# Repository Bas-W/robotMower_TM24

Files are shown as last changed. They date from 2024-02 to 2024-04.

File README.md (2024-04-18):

# robotMower_TM24
Robot lawn mower project for school.

# Notes
Some notes including the lessons we learned and the mistakes we found in our work can be found under [<b>*/Notes*</b>](/Notes.md)\
This contains some important information for anyone who wants to expand this project, **Please read this document**.

# Features
A list of features can be found under [<b>*/Features*</b>](/Features.md)

# Schematics, PCB
Schematics, along with footprints, can be found under [<b>*/Schematics*</b>](/Schematics).
These are designed in Fusion 360/Eagle, original Fusion/eagle Schematic, board and library files can be found under [***/Schematics/RoborMower_TM24/***](/Schematics/RoborMower_TM24/)

# Code
Code can be found under [***/Code***](/Code).
The final code for the ESP32 can be found under [***/Code/Final_V1.0***](/Code/Final_V1.0.0/).
The final code for the Attiny that read the HC-SR04 sensor can be fount under [***/Code/Test Sketches/ATtiny84_I2C-Slave-Ultrasonic_Test/***](/Code/Test%20Sketches/ATtiny84_I2C-Slave-Ultrasonic_Test/).

# Harware
A list of used components and modules will be made when the design is finalized.

# I²C Adress List
|Part|Address|
|----|---|
|Current Sensor, Motor L|01000000 = 0x40|
|Current Sensor, Motor R|01000001 = 0x41|
|Current Sensor, Bat in|01000010 = 0x42|
|Current Sensor, 5V|01000011 = 0x43|
|Current Sensor, 3V3|01000100 = 0x44|
|Attiny, Ultrasone Sensors|00001000 = 0x8|

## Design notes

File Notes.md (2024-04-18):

# Belangrijke info / gemaakte fouten

# Motor driver
*Gemaakt door Bas Welters.*

Voor dit project maakten we zelf een H-brug om de motors aan te sturen.
Deze H-brug is opgesteld uit MOSFETs en zou aangestuurd worden via een Attiny die op een I²C-bus aangesloten is.

Bij het ontwerpen van de H-brug koos ik echter voor de foute soort MOSFET's voor de high-side switches. Ik gebruik hiervoor NPN-MOSFET's i.p.v. PNP-MOSFET's.
Het ontwerp werkte om de motors aan te sturen maar ik kon niet genoeg spanning doorlaten omdat de gate-spanning op de high-side MOSFET's niet hoog genoeg was. (5V i.p.v. groter dan 12V).
We kozen ervoor om een pre-made H-brug te gebruiken maar het zou wel handig geweest zijn om onze eigen module te gebruiken.
Op de motor driver staan ook twee IC's om het stroomverbruik en de spanning te meten voor elke motor.

# Power-board
*Gemaakt door Bas Welters.*

Op het power-board wordt de batterijspanning omgezet naar 5v en 3.3V.
Dit doen we met LM1117T IC's.
Het bord is bedoeld om gevoedt te worden door een 3S LIPO-batterij.

Om de cellen van de batterij apart uit te meten is ook een JST-poort voorzien. Deze kan echter nog niet gebruikt worden omdat de spanning te hoog is om rechtstreeks uit te lezen met de Attiny.
Om deze poort te kunnen gebruiken zou een tussenstuk gemaakt kunnen worden met spanningsdelers om de spanning binnnen het bereik van de Attiny te brengen.
De Attiny op het power-bord kan met de ESP-32 communiceren via de I²C-bus.

# MCU
*Gemaakt door Nick Bosschaert*

Het MCU-board is de brains van de Robot Mower. Hier worden alle signalen van de sensoren ontvangen en worden alle actuatoren naar behoren aangestuurd. De microcontroller die we plaatsten op dit board is de *ESP32S3 Wroom-1-N8R8*. Dit is de chip die gebruikt wordt op het esp32s3 development board.

Aangezien er eerst voorzien was om een custom H-brug te maken en deze via I²C te verbinden waren er geen connecties voorzien om de originele H-brug te gebruiken. Er zijn echter nog wat extra IO-pins voorzien voor uitbreidingen, deze pins konden we dus gebruiken om de H-brug rechtstreeks aan te sturen met de ESP.

Alle communicatie tussen de mcu en de andere componenten zoals powerboard, hc-sr04 ultrasonic sensors, etc. wordt mogelijk gemaakt door een I²C bus. Deze bus laat ons toe om zowel berichten te ontvangen als te sturen naar geconnecteerde devices. De bus-connector bevat zowel een 5V als 3V3 pin om het gebruik van verschillende sensoren mogelijk te maken. Deze bus wordt dus ook gebruikt om de externe modules van stroom te voorzien.
De SCL en SDA lijnen van deze bus hebben zoals het hoort een pullup naar 3V3. Verbindt deze lijnen **NOOIT** met 5V, want dan zal de esp32 kortgesloten worden. Aangezien I²C werkt met een pulldown om een digitale 1 door te sturen, is dit geen probleem zolang de devices op de bus een digitale 1 lezen op een lager voltage dan 3V3.

Dit board bevat ook een USB-B connector. Deze wordt gebruikt voor het uploaden van nieuwe programmas naar de ESP32 en om gebruik te maken van de seriële monitor.

Veel sensoren en IC's werken met I²C, maar er is ook een connector voorzien voor SPI om bijvoorbeeld een SD-Card te gebruiken om data op op te slaan.

# HC-SR04 Ultrasonic Sensor
*Gemaakt door Nick Bosschaert*

Dit board zorgt ervoor dat er wat druk van de MCU afgehaald wordt door de 3 HC-SR04 afstandssensoren in te laten lezen door een ATTiny. Hierdoor kan het programma op de ESP32 verkleind en de werkdruk verlaagd worden.

De Attiny heeft zelf geen interne timer, waardoor de sensoren niet op de normale manier uitgelezen kunnen worden. Daarom wordt de "NewPing" library gebruikt, deze library laat je toe om toch een timer te gebruiken op de Attiny.
Als de MCU dan een request doet voor 11 bytes aan data, dan stuurt de ATTINY dit geformatteerd door.
Het is tot op heden nog niet mogelijk om een serial output te krijgen van de attiny, een mogelijke oplossing zou zijn om virtueel een UART poort aan te maken en deze via de UART-to-USB chip van een arduino uno of dergelijke te laten gaan.

Het pcb is heel basic met enkel het broodnodige voor de ATTiny om te kunnen draaien, de 2 I²C connectors om door te kunnen verbinden en de 3 connectors voor de HC-SR04 afstandssensoren. Behalve dan dat de lay-out verbeterd zou kunnen worden, is dit een geslaagd ontwerp.

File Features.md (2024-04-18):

# robotMower_TM24
Robot lawn mower project for school.

# Possible Components

|Component|Feature|Digital IO|Analog IO|Multiply|
|---|---|---|---|---|
|HC-SR04 Ultra Sonic|Collision Avoidance|2|0|3|
|Bumper Microswitch|Collision Detection|1|0|2|
|LCD|Interface|2 I2C|0|1|
|Control buttons|Interface|1|0|4|
|Voltage Meter/resistors|Battery Percentage Readout|0|1|1|
|Blades motor|Grass Cutting|3|0|1
|Motor Driver|Driving|6|0|1|
|RTC|Time Control|2 I2C|0|1|
|QMC5883 Kompas||2 I2C|0|1|
|Rocker Switch|Main Power Switch|0|0|1|
|Relay|Emergency Stop/Power Cutoff|2|0|1|
|Axial sensor|Tilt Sensor|x|x|1|
|LM1117 T5.0 LDO|5V Regulation|0|0|1|
|LM1117 T3.3 LDO|3V Regulation|0|0|1|
|Water Sensor|Rain Detection|0|1|1|
|ATtiny84|Breakout µControllers|2 I2C|0|2|
|USB-B|USB-Port|2|0|1|

# Current Features
- [x] Internal 5V Regulation
- [x] Internal 3V3 Regulation
- [x] Current, Voltage, Wattage sensing Battery power
- [x] Current, Voltage, Wattage sensing 5V power
- [x] Current, Voltage, Wattage sensing 3V3 power
- [x] Custom PCB
- [x] Easily Controllable Interface (lcd/oled etc)
- [x] Main Power switch
- [x] USB-connector for programming & monitoring (USB-B / USB-C)
- [x] JST
- [x] Seperate boards - connected via [5v,3v3,I²C]bus
  - MCU
  - Power
  - Sensors

# Possible Features
- [ ] Driving
- [ ] Grass Cutting
- [ ] Power cutoff relay to take away power to motors / emergency stop button (in case of rogue robot event) 
- [ ] Current Measuring for wheels
- [ ] Current Measuring for Blade
- [ ] Collision Avoidance
- [ ] Collision Detection
- [ ] Rain Detection
- [ ] Time Control
- [ ] Small Formfactor
- [ ] Power supply -> 3S/4S LiPo pack ?
- [ ] Battery Charging
- [ ] Battery Percentage Readout
- [ ] Extra I-O for expansions
- [ ] Tilt sensor/switches 
- [ ] Custom H-bridge
- [ ] SD-card slot
- [ ] Temperature sensors for motors (expansion)
- [ ] Temperature sensors for motor drivers (expansion)
- [ ] GPS (u-blox module) (expansion)
- [ ] Perimeter wire (expansion)

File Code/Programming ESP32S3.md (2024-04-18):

# How to Program the ESP32S3 Wroom 1 N8R8

## Connections to ESP32 Dev module
### UART
|ESP32S3|ESP32 Dev Module|
|---|---|
|3V3|3V3|
|GND|GND|
|RX|RX|
|TX|TX|

Connect the ESP32 Dev Module's EN pin to GND.

### USB
Or you can use the USB-B jack to connect straight to your laptop.
Don't forget to enable ***USB CDC On Boot*** in the tools menu.

## Programming ESP32S3
Board: ESP32S3 Dev Module

1. Press and hold the Boot Button.
2. Press and Release the EN/Reset Button.
3. Release the Boot Button.

Upload the program to the ESP32 Dev Module and after the upload is compleet, press the reset button once more so that the ESP32S3 will be reset.

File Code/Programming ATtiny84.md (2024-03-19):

# How to Program the ATtiny84

[example](https://www.instructables.com/Arduino-Uno-to-Program-ATTINY84-Arduino-V-185/)

## Setup
Additional boards: http://drazzy.com/package_drazzy.com_index.json
Upload the ArduinoISP sketch from the example sketches to the Uno.

## Connections to UNO
|ATtiny84|UNO|
|---|---|
|5V|5V|
|GND|GND|
|Pin4|Pin10|
|Pin7|Pin11|
|Pin8|Pin12|
|Pin9|Pin13|

Connect UNO RESET pin to GND via 10uF Elec Cap.

## Programming ATtiny84
Board: ATtiny84
B.O.D.: Disable
LTO: Disable
Pin Mapping: Counter Clockwise
Chip: ATtiny84
Clock: 8MHz Internal
Bootloader: Burn Bootloader
Programmer: Arduino as ISP

To program the attiny you have to use *Upload Using Programmer* or shortcut *Ctrl + Shift + U* otherwise the preselected programmer won't be used.

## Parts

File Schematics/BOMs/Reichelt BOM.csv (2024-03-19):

Qty | Ultrasonic | MCU | Motor | Power | Reserve | Value | Device | Package | Parts | Description | MANUFACTURER_NAME | MANUFACTURER_PART_NUMBER | Reichelt_PART_NUMBER
7 | 3 |  |  | 1 | 3 | JST XH 4-PIN | JST-XH-04-PIN-LONG-PAD | JST-XH-04-PACKAGE-LONG-PAD |  |  |  |  | JST XH4P ST
7 | 3 |  |  | 1 | 3 | Female |  |  |  |  |  |  | JST XH4P BU
15 | 2 | 4 | 2 | 2 | 5 | JST XH 5-PIN | JST-XH-05-PIN-LONG-PAD | JST-XH-05-PACKAGE-LONG-PAD |  |  |  |  | JST XH5P ST
15 | 2 | 4 | 2 | 2 | 5 | Female |  |  |  |  |  |  | JST XH5P BU
66 | 22 | 20 | 10 | 14 | 34 | Krimp Klipkes |  |  |  |  |  |  | JST XH CKB

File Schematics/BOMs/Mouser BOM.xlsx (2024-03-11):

Qty | Ultrasonic | MCU | Motor | Power | Reserve | Value | Device | Package | Parts | Description | MANUFACTURER_NAME | MANUFACTURER_PART_NUMBER | MOUSER_PART_NUMBER
20 | 2 | 3 | 4 | 5 | 6 | 0.1uF | C-EU025-030X050 | C025-030X050 | CAPACITOR, European symbol |  | Murata Electronics | RDER71E104K0P1H03B | 81-RDER71E104K0P1H3B
10 | 1 | 1 | 1 | 5 | 2 | 10uF | CPOL-EUE5-10.5 | E5-10,5 | POLARIZED CAPACITOR, European symbol |  | Würth Elektronik | "870575873001" | 710-870575873001
10 |  |  | 2 | 3 | 5 | 220Ohm | R-EU_0204/7 | 0204/7 | RESISTOR, European symbol |  | KOA Speer (https://www.mouser.be/manufacturer/koa-speer/) | MF1/4CCT52R2200F | 660-MF1/4CCT52R2200F
10 | 1 | 2 | 1 | 1 | 5 | 10kOhm | R-EU_0204/7 | 0204/7 | RESISTOR, European symbol |  | KOA Speer (https://www.mouser.be/manufacturer/koa-speer/) | MF1/4LCT52R103G | 660-MF1/4LCT52R103G
5 |  | 2 |  |  | 3 | 2k2 | R-EU_0204/5 | 0204/5 | RESISTOR, European symbol |  | KOA Speer (https://www.mouser.be/manufacturer/koa-speer/) | MF1/4DCT52R2201F | 660-MF1/4DCT52R2201F
6 |  |  | 2 | 2 | 2 | 12mOhm | R-EU_0204/7 | 0204/7 | RESISTOR, European symbol |  | YAGEO | ERJ-6CWDR012V | 667-ERJ-6CWDR012V
5 |  |  |  | 2 | 3 | 39mOhm | R-EU_0204/7 | 0204/7 | RESISTOR, European symbol |  | YAGEO | PE2512DKE070R04L | 603-PE2512DKE070R04L
2 |  | 1 |  |  | 1 | USB_B_PTH | USB-B-PTH | USB Type B Connector |  |  | CUI Devices | UJ2-B-HR-G-TH | 179-UJ2-B-HR-G-TH
10 | 1 | 2 | 1 | 1 | 5 | button | SWITCH_PUSHBUTTONEVQ-PE | TACT_PANA-EVQ | Buttons |  | TE Connectivity / Alcoswitch | FSMCH | 506-FSMCH
5 | 1 |  | 1 | 1 | 2 | ATtiny84DIP | ATTINY84DIP | ATTINY84(DIP) |  |  | Microchip Technology | ATTINY84A-PU | 556-ATTINY84A-PU
5 | 1 |  | 1 | 1 | 2 | 14Pin IC Socket |  |  |  |  | TE Connectivity | 1-2199298-3 | 571-1-2199298-3
2 |  | 1 |  |  | 1 | ESP32-S3-WROOM-1 | ESP32-S3-WROOM-1 |  |  |  | Espressif Systems | ESP32-S3-WROOM-1-N8R8 | 356-EP32S3WROOM1N8R8
8 |  |  | 2 | 3 | 3 | INA219BIDR | SOIC127P600X175-8N | 26-V, Bidirectional, Zero-Drift, High-Side, I2C Out Current/Power Monitor |  |  | Texas Instruments | INA219BIDR | 595-INA219BIDR
12 |  | 1 | 8 |  | 3 | IRFB7430PBF | TO254P483X1016X1994-3P | Infineon IRFB7430PBF N-channel MOSFET, 195 A, 40 V StrongIRFET, 3-Pin TO-220AB |  |  | Infineon Technologies | IRFB7430PBF | 942-IRFB7430PBF
2 |  |  |  | 1 | 1 | LM1117T-5.0_NOPB | TO254P470X1028X1955-3P | Space saving 800-mA low-dropout linear regulator with internal current limit |  |  | Texas Instruments | LM1117T-5.0/NOPB | 926-LM1117T-50/NOPB
2 |  |  |  | 1 | 1 | LM1117T-3.3_NOPB | TO254P470X1028X1955-3P | 800mA,3.3V,LDO Voltage Reg.,LM1117T-3.3 Texas Instruments LM1117T-3.3/NOPB, LDO Voltage Regulator, 800mA, 3.3 V |  |  | Texas Instruments | LM1117T-3.3/NOPB | 926-LM1117T-3.3/NOPB

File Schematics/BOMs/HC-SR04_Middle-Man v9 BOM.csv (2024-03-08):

Part | Value | Device | Package | Description | POPULARITY | SPICEPREFIX
C3 | 0.1uF | C-EU025-030X050 | C025-030X050 | CAPACITOR, European symbol | 14 | C
C9 | 0.1uF | C-EU025-025X050 | C025-025X050 | CAPACITOR, European symbol | 65 | C
C10 | 10uF | CPOL-EUE5-10.5 | E5-10,5 | POLARIZED CAPACITOR, European symbol | 23 | C
H1 | MOUNT-PAD-ROUND3.3 | MOUNT-PAD-ROUND3.3 | 3,3-PAD | MOUNTING PAD, round | 1
H2 | MOUNT-PAD-ROUND3.3 | MOUNT-PAD-ROUND3.3 | 3,3-PAD | MOUNTING PAD, round | 1
H3 | MOUNT-PAD-ROUND3.3 | MOUNT-PAD-ROUND3.3 | 3,3-PAD | MOUNTING PAD, round | 1
H4 | MOUNT-PAD-ROUND3.3 | MOUNT-PAD-ROUND3.3 | 3,3-PAD | MOUNTING PAD, round | 1
HC-SR04-L | LEFT_Sonic | JST-XH-04-PIN-LONG-PAD | JST-XH-04-PACKAGE-LONG-PAD | JST XH Connector 2 Pin
HC-SR04-M | Mid_Sonic | JST-XH-04-PIN-LONG-PAD | JST-XH-04-PACKAGE-LONG-PAD | JST XH Connector 2 Pin
HC-SR04-R | Right_Sonic | JST-XH-04-PIN-LONG-PAD | JST-XH-04-PACKAGE-LONG-PAD | JST XH Connector 2 Pin
JST-XH1 | I2C-BUS | JST-XH-05-PIN-LONG-PAD | JST-XH-05-PACKAGE-LONG-PAD | JST XH Connector 2 Pin
JST-XH2 | I2C-BUS | JST-XH-05-PIN-LONG-PAD | JST-XH-05-PACKAGE-LONG-PAD | JST XH Connector 2 Pin
R4 | 10k | R-EU_0204/7 | 0204/7 | RESISTOR, European symbol | 79 | R
RESET |  | SWITCH_PUSHBUTTONEVQ-PE | TACT_PANA-EVQ | Buttons
U$3 | ATTINY84DIP | ATTINY84DIP | ATTINY84(DIP)

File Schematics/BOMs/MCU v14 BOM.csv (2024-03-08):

Part | Value | Device | Package | Description | CATEGORY | MANUFACTURER | MPN | OPERATING_TEMP | PART_STATUS | POPULARITY | PROD_ID | ROHS_COMPLIANT | SERIES | SF_ID | SPICEPREFIX | SUB-CATEGORY | THERMALLOSS | TYPE | VOLTAGE_RATING
BOOT |  | SWITCH_PUSHBUTTONEVQ-PE | TACT_PANA-EVQ | Buttons
BUTTONS | Control Buttons | JST-XH-05-PIN-LONG-PAD | JST-XH-05-PACKAGE-LONG-PAD | JST XH Connector 2 Pin
C3 | 0.1uF | C-EU025-030X050 | C025-030X050 | CAPACITOR, European symbol |  |  |  |  |  | 14 |  |  |  |  | C
C4 | 0.1uF | C-EU025-030X050 | C025-030X050 | CAPACITOR, European symbol |  |  |  |  |  | 14 |  |  |  |  | C
C6 | 10uF | C-POL_RADIAL-11MM-DIA | CAPPRD508W65D1000H1100B | Capacitor Polarised - Generic | Capacitor
C7 | TBD | C-EU025-030X050 | C025-030X050 | CAPACITOR, European symbol |  |  |  |  |  | 14 |  |  |  |  | C
C8 | TBD | C-EU025-030X050 | C025-030X050 | CAPACITOR, European symbol |  |  |  |  |  | 14 |  |  |  |  | C
C23 | 0.1uF | C-EU025-030X050 | C025-030X050 | CAPACITOR, European symbol |  |  |  |  |  | 14 |  |  |  |  | C
H1 | MOUNT-PAD-ROUND3.3 | MOUNT-PAD-ROUND3.3 | 3,3-PAD | MOUNTING PAD, round |  |  |  |  |  | 1
H2 | MOUNT-PAD-ROUND3.3 | MOUNT-PAD-ROUND3.3 | 3,3-PAD | MOUNTING PAD, round |  |  |  |  |  | 1
H3 | MOUNT-PAD-ROUND3.3 | MOUNT-PAD-ROUND3.3 | 3,3-PAD | MOUNTING PAD, round |  |  |  |  |  | 1
H4 | MOUNT-PAD-ROUND3.3 | MOUNT-PAD-ROUND3.3 | 3,3-PAD | MOUNTING PAD, round |  |  |  |  |  | 1
J1 | USB_B_PTH | USB_B_PTH | USB-B-PTH | USB Type B Connector |  |  |  |  |  |  | CONN-08278 |  |  | PRT-00139
JP2 |  | PINHD-1X2 | 1X02 | PIN HEADER |  |  |  |  |  | 98
JP3 |  | PINHD-1X55X2MM | 1_05X2MM | PIN HEADER |  |  |  |  |  | 0
JP4 |  | PINHD-1X8 | 1X08 | PIN HEADER |  |  |  |  |  | 67
JP5 |  | PINHD-1X4 | 1X04 | PIN HEADER |  |  |  |  |  | 91
JST-XH2 | I2C-BUS | JST-XH-05-PIN-LONG-PAD | JST-XH-05-PACKAGE-LONG-PAD | JST XH Connector 2 Pin
JST-XH3 | I2C-BUS | JST-XH-05-PIN-LONG-PAD | JST-XH-05-PACKAGE-LONG-PAD | JST XH Connector 2 Pin
R1 | 2k2 | R-EU_0204/5 | 0204/5 | RESISTOR, European symbol |  |  |  |  |  | 35 |  |  |  |  | R
R2 | 2k2 | R-EU_0204/5 | 0204/5 | RESISTOR, European symbol |  |  |  |  |  | 35 |  |  |  |  | R
R3 | 10k | R-EU_0204/7 | 0204/7 | RESISTOR, European symbol |  |  |  |  |  | 79 |  |  |  |  | R
R6 | 10k | R-EU_0204/7 | 0204/7 | RESISTOR, European symbol |  |  |  |  |  | 79 |  |  |  |  | R
RESET |  | SWITCH_PUSHBUTTONEVQ-PE | TACT_PANA-EVQ | Buttons
SPI | SPI-Header | JST-XH-07-PIN-LONG-PAD | JST-XH-07-PACKAGE-LONG-PAD | JST XH Connector 2 Pin
U$1 | ESP32-S3-WROOM-1 | ESP32-S3-WROOM-1 | ESP32-S3-WROOM-1
UART1 | UART | JST-XH-05-PIN-ROUND-PAD | JST-XH-05-PACKAGE-ROUND-PAD | JST XH Connector 2 Pin

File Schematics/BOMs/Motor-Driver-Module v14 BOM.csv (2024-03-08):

Part | Value | Device | Package | Description | ARROW_PART_NUMBER | ARROW_PRICE-STOCK | DESCRIPTION | HEIGHT | MANUFACTURER_NAME | MANUFACTURER_PART_NUMBER | MOUSER_PART_NUMBER | MOUSER_PRICE-STOCK | POPULARITY | SPICEPREFIX
C1 | 0.1uF | C-EU025-025X050 | C025-025X050 | CAPACITOR, European symbol |  |  |  |  |  |  |  |  | 65 | C
C2 | 10uF | CPOL-EUE5-10.5 | E5-10,5 | POLARIZED CAPACITOR, European symbol |  |  |  |  |  |  |  |  | 23 | C
C3 | 0.1uF | C-EU025-030X050 | C025-030X050 | CAPACITOR, European symbol |  |  |  |  |  |  |  |  | 14 | C
C4 | 0.1uF | C-EU025-030X050 | C025-030X050 | CAPACITOR, European symbol |  |  |  |  |  |  |  |  | 14 | C
C5 | 0.1uF | C-EU025-030X050 | C025-030X050 | CAPACITOR, European symbol |  |  |  |  |  |  |  |  | 14 | C
D1 |  | SCHOTTKY-DIODEDO41 | DO41-10 | Schottky Diode
D2 |  | SCHOTTKY-DIODEDO41 | DO41-10 | Schottky Diode
D3 |  | SCHOTTKY-DIODEDO41 | DO41-10 | Schottky Diode
D4 |  | SCHOTTKY-DIODEDO41 | DO41-10 | Schottky Diode
D5 |  | SCHOTTKY-DIODEDO41 | DO41-10 | Schottky Diode
D6 |  | SCHOTTKY-DIODEDO41 | DO41-10 | Schottky Diode
D7 |  | SCHOTTKY-DIODEDO41 | DO41-10 | Schottky Diode
D8 |  | SCHOTTKY-DIODEDO41 | DO41-10 | Schottky Diode
H1 | MOUNT-PAD-ROUND3.3 | MOUNT-PAD-ROUND3.3 | 3,3-PAD | MOUNTING PAD, round |  |  |  |  |  |  |  |  | 1
H2 | MOUNT-PAD-ROUND3.3 | MOUNT-PAD-ROUND3.3 | 3,3-PAD | MOUNTING PAD, round |  |  |  |  |  |  |  |  | 1
H3 | MOUNT-PAD-ROUND3.3 | MOUNT-PAD-ROUND3.3 | 3,3-PAD | MOUNTING PAD, round |  |  |  |  |  |  |  |  | 1
H4 | MOUNT-PAD-ROUND3.3 | MOUNT-PAD-ROUND3.3 | 3,3-PAD | MOUNTING PAD, round |  |  |  |  |  |  |  |  | 1
IC1 | INA219BIDR | INA219BIDR | SOIC127P600X175-8N | 26-V, Bidirectional, Zero-Drift, High-Side, I2C Out Current/Power Monitor |  |  | 26-V, Bidirectional, Zero-Drift, High-Side, I2C Out Current/Power Monitor | 1.75mm | Texas Instruments | INA219BIDR | 595-INA219BIDR | https://www.mouser.co.uk/ProductDetail/Texas-Instruments/INA219BIDR?qs=1WmUhT%2FVMINyGsXNJcdD5Q%3D%3D
IC2 | INA219BIDR | INA219BIDR | SOIC127P600X175-8N | 26-V, Bidirectional, Zero-Drift, High-Side, I2C Out Current/Power Monitor |  |  | 26-V, Bidirectional, Zero-Drift, High-Side, I2C Out Current/Power Monitor | 1.75mm | Texas Instruments | INA219BIDR | 595-INA219BIDR | https://www.mouser.co.uk/ProductDetail/Texas-Instruments/INA219BIDR?qs=1WmUhT%2FVMINyGsXNJcdD5Q%3D%3D
JST-XH1 | I2C-BUS | JST-XH-05-PIN-LONG-PAD | JST-XH-05-PACKAGE-LONG-PAD | JST XH Connector 2 Pin
JST-XH2 | I2C-BUS | JST-XH-05-PIN-LONG-PAD | JST-XH-05-PACKAGE-LONG-PAD | JST XH Connector 2 Pin
MOTOR-L | 1747993 | 1747993 | 1747993 | PCB header, nominal cross section: 2.5 mm?, color: green, nominal current: 12 A, rated voltage (III/2): 320 V, contact surface: Gold, type of contact: Male connector, Number of potentials: 2, Number of rows: 1, Number of positions per row: 2, number of connections: 2, product range: MSTBVA 2,5/..-G, pitch: 5.08 mm, mounting: Wave soldering, pin layout: Linear pinning, solder pin [P]: 3.9 mm, Stecksystem: CLASSIC COMBICON, Locking: without, type of packaging: packed in cardboard |  |  | PCB header, nominal cross section: 2.5 mm?, color: green, nominal current: 12 A, rated voltage (III/2): 320 V, contact surface: Gold, type of contact: Male connector, Number of potentials: 2, Number of rows: 1, Number of positions per row: 2, number of connections: 2, product range: MSTBVA 2,5/..-G, pitch: 5.08 mm, mounting: Wave soldering, pin layout: Linear pinning, solder pin [P]: 3.9 mm, Stecksystem: CLASSIC COMBICON, Locking: without, type of packaging: packed in cardboard | 12.15mm | Phoenix Contact | 1747993 | 651-1747993 | https://www.mouser.co.uk/ProductDetail/Phoenix-Contact/1747993?qs=cq3Rj917t3li0%2FrJTXaRgg%3D%3D
MOTOR-R | 1747993 | 1747993 | 1747993 | PCB header, nominal cross section: 2.5 mm?, color: green, nominal current: 12 A, rated voltage (III/2): 320 V, contact surface: Gold, type of contact: Male connector, Number of potentials: 2, Number of rows: 1, Number of positions per row: 2, number of connections: 2, product range: MSTBVA 2,5/..-G, pitch: 5.08 mm, mounting: Wave soldering, pin layout: Linear pinning, solder pin [P]: 3.9 mm, Stecksystem: CLASSIC COMBICON, Locking: without, type of packaging: packed in cardboard |  |  | PCB header, nominal cross section: 2.5 mm?, color: green, nominal current: 12 A, rated voltage (III/2): 320 V, contact surface: Gold, type of contact: Male connector, Number of potentials: 2, Number of rows: 1, Number of positions per row: 2, number of connections: 2, product range: MSTBVA 2,5/..-G, pitch: 5.08 mm, mounting: Wave soldering, pin layout: Linear pinning, solder pin [P]: 3.9 mm, Stecksystem: CLASSIC COMBICON, Locking: without, type of packaging: packed in cardboard | 12.15mm | Phoenix Contact | 1747993 | 651-1747993 | https://www.mouser.co.uk/ProductDetail/Phoenix-Contact/1747993?qs=cq3Rj917t3li0%2FrJTXaRgg%3D%3D
PWR | GN | LED5MM | LED5MM | LED
Q1 | IRFB7430PBF | IRFB7430PBF | TO254P483X1016X1994-3P | Infineon IRFB7430PBF N-channel MOSFET, 195 A, 40 V StrongIRFET, 3-Pin TO-220AB |  |  | Infineon IRFB7430PBF N-channel MOSFET, 195 A, 40 V StrongIRFET, 3-Pin TO-220AB | 4.83mm | Infineon | IRFB7430PBF | 942-IRFB7430PBF | https://www.mouser.co.uk/ProductDetail/Infineon-Technologies/IRFB7430PBF?qs=PRpJrl6HpdwkCaEhLAouSA%3D%3D
Q2 | IRFB7430PBF | IRFB7430PBF | TO254P483X1016X1994-3P | Infineon IRFB7430PBF N-channel MOSFET, 195 A, 40 V StrongIRFET, 3-Pin TO-220AB |  |  | Infineon IRFB7430PBF N-channel MOSFET, 195 A, 40 V StrongIRFET, 3-Pin TO-220AB | 4.83mm | Infineon | IRFB7430PBF | 942-IRFB7430PBF | https://www.mouser.co.uk/ProductDetail/Infineon-Technologies/IRFB7430PBF?qs=PRpJrl6HpdwkCaEhLAouSA%3D%3D
Q3 | IRFB7430PBF | IRFB7430PBF | TO254P483X1016X1994-3P | Infineon IRFB7430PBF N-channel MOSFET, 195 A, 40 V StrongIRFET, 3-Pin TO-220AB |  |  | Infineon IRFB7430PBF N-channel MOSFET, 195 A, 40 V StrongIRFET, 3-Pin TO-220AB | 4.83mm | Infineon | IRFB7430PBF | 942-IRFB7430PBF | https://www.mouser.co.uk/ProductDetail/Infineon-Technologies/IRFB7430PBF?qs=PRpJrl6HpdwkCaEhLAouSA%3D%3D
Q4 | IRFB7430PBF | IRFB7430PBF | TO254P483X1016X1994-3P | Infineon IRFB7430PBF N-channel MOSFET, 195 A, 40 V StrongIRFET, 3-Pin TO-220AB |  |  | Infineon IRFB7430PBF N-channel MOSFET, 195 A, 40 V StrongIRFET, 3-Pin TO-220AB | 4.83mm | Infineon | IRFB7430PBF | 942-IRFB7430PBF | https://www.mouser.co.uk/ProductDetail/Infineon-Technologies/IRFB7430PBF?qs=PRpJrl6HpdwkCaEhLAouSA%3D%3D
Q5 | IRFB7430PBF | IRFB7430PBF | TO254P483X1016X1994-3P | Infineon IRFB7430PBF N-channel MOSFET, 195 A, 40 V StrongIRFET, 3-Pin TO-220AB |  |  | Infineon IRFB7430PBF N-channel MOSFET, 195 A, 40 V StrongIRFET, 3-Pin TO-220AB | 4.83mm | Infineon | IRFB7430PBF | 942-IRFB7430PBF | https://www.mouser.co.uk/ProductDetail/Infineon-Technologies/IRFB7430PBF?qs=PRpJrl6HpdwkCaEhLAouSA%3D%3D
Q6 | IRFB7430PBF | IRFB7430PBF | TO254P483X1016X1994-3P | Infineon IRFB7430PBF N-channel MOSFET, 195 A, 40 V StrongIRFET, 3-Pin TO-220AB |  |  | Infineon IRFB7430PBF N-channel MOSFET, 195 A, 40 V StrongIRFET, 3-Pin TO-220AB | 4.83mm | Infineon | IRFB7430PBF | 942-IRFB7430PBF | https://www.mouser.co.uk/ProductDetail/Infineon-Technologies/IRFB7430PBF?qs=PRpJrl6HpdwkCaEhLAouSA%3D%3D
Q7 | IRFB7430PBF | IRFB7430PBF | TO254P483X1016X1994-3P | Infineon IRFB7430PBF N-channel MOSFET, 195 A, 40 V StrongIRFET, 3-Pin TO-220AB |  |  | Infineon IRFB7430PBF N-channel MOSFET, 195 A, 40 V StrongIRFET, 3-Pin TO-220AB | 4.83mm | Infineon | IRFB7430PBF | 942-IRFB7430PBF | https://www.mouser.co.uk/ProductDetail/Infineon-Technologies/IRFB7430PBF?qs=PRpJrl6HpdwkCaEhLAouSA%3D%3D
Q8 | IRFB7430PBF | IRFB7430PBF | TO254P483X1016X1994-3P | Infineon IRFB7430PBF N-channel MOSFET, 195 A, 40 V StrongIRFET, 3-Pin TO-220AB |  |  | Infineon IRFB7430PBF N-channel MOSFET, 195 A, 40 V StrongIRFET, 3-Pin TO-220AB | 4.83mm | Infineon | IRFB7430PBF | 942-IRFB7430PBF | https://www.mouser.co.uk/ProductDetail/Infineon-Technologies/IRFB7430PBF?qs=PRpJrl6HpdwkCaEhLAouSA%3D%3D
R1 | 12m | R-EU_0204/7 | 0204/7 | RESISTOR, European symbol |  |  |  |  |  |  |  |  | 79 | R
R2 | 12m | R-EU_0204/7 | 0204/7 | RESISTOR, European symbol |  |  |  |  |  |  |  |  | 79 | R
R3 | 10k | R-EU_0204/7 | 0204/7 | RESISTOR, European symbol |  |  |  |  |  |  |  |  | 79 | R
R4 | 220 | R-EU_0204/7 | 0204/7 | RESISTOR, European symbol |  |  |  |  |  |  |  |  | 79 | R
R5 | 220 | R-EU_0204/7 | 0204/7 | RESISTOR, European symbol |  |  |  |  |  |  |  |  | 79 | R
RESET |  | SWITCH_PUSHBUTTONEVQ-PE | TACT_PANA-EVQ | Buttons
STATUS | RD | LED5MM | LED5MM | LED
SUPPLY | 1747993 | 1747993 | 1747993 | PCB header, nominal cross section: 2.5 mm?, color: green, nominal current: 12 A, rated voltage (III/2): 320 V, contact surface: Gold, type of contact: Male connector, Number of potentials: 2, Number of rows: 1, Number of positions per row: 2, number of connections: 2, product range: MSTBVA 2,5/..-G, pitch: 5.08 mm, mounting: Wave soldering, pin layout: Linear pinning, solder pin [P]: 3.9 mm, Stecksystem: CLASSIC COMBICON, Locking: without, type of packaging: packed in cardboard |  |  | PCB header, nominal cross section: 2.5 mm?, color: green, nominal current: 12 A, rated voltage (III/2): 320 V, contact surface: Gold, type of contact: Male connector, Number of potentials: 2, Number of rows: 1, Number of positions per row: 2, number of connections: 2, product range: MSTBVA 2,5/..-G, pitch: 5.08 mm, mounting: Wave soldering, pin layout: Linear pinning, solder pin [P]: 3.9 mm, Stecksystem: CLASSIC COMBICON, Locking: without, type of packaging: packed in cardboard | 12.15mm | Phoenix Contact | 1747993 | 651-1747993 | https://www.mouser.co.uk/ProductDetail/Phoenix-Contact/1747993?qs=cq3Rj917t3li0%2FrJTXaRgg%3D%3D
U$1 | ATTINY84DIP | ATTINY84DIP | ATTINY84(DIP)

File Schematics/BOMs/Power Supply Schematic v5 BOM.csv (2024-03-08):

Part | Value | Device | Package | Description | ARROW_PART_NUMBER | ARROW_PRICE-STOCK | DESCRIPTION | HEIGHT | MANUFACTURER_NAME | MANUFACTURER_PART_NUMBER | MOUSER2_PART_NUMBER | MOUSER2_PRICE-STOCK | MOUSER_PART_NUMBER | MOUSER_PRICE-STOCK | POPULARITY | SPICEPREFIX
BAT-IN | 1747993 | 1747993 | 1747993 | PCB header, nominal cross section: 2.5 mm?, color: green, nominal current: 12 A, rated voltage (III/2): 320 V, contact surface: Gold, type of contact: Male connector, Number of potentials: 2, Number of rows: 1, Number of positions per row: 2, number of connections: 2, product range: MSTBVA 2,5/..-G, pitch: 5.08 mm, mounting: Wave soldering, pin layout: Linear pinning, solder pin [P]: 3.9 mm, Stecksystem: CLASSIC COMBICON, Locking: without, type of packaging: packed in cardboard |  |  | PCB header, nominal cross section: 2.5 mm?, color: green, nominal current: 12 A, rated voltage (III/2): 320 V, contact surface: Gold, type of contact: Male connector, Number of potentials: 2, Number of rows: 1, Number of positions per row: 2, number of connections: 2, product range: MSTBVA 2,5/..-G, pitch: 5.08 mm, mounting: Wave soldering, pin layout: Linear pinning, solder pin [P]: 3.9 mm, Stecksystem: CLASSIC COMBICON, Locking: without, type of packaging: packed in cardboard | 12.15mm | Phoenix Contact | 1747993 |  |  | 651-1747993 | https://www.mouser.co.uk/ProductDetail/Phoenix-Contact/1747993?qs=cq3Rj917t3li0%2FrJTXaRgg%3D%3D
BAT-OUT1 | 1747993 | 1747993 | 1747993 | PCB header, nominal cross section: 2.5 mm?, color: green, nominal current: 12 A, rated voltage (III/2): 320 V, contact surface: Gold, type of contact: Male connector, Number of potentials: 2, Number of rows: 1, Number of positions per row: 2, number of connections: 2, product range: MSTBVA 2,5/..-G, pitch: 5.08 mm, mounting: Wave soldering, pin layout: Linear pinning, solder pin [P]: 3.9 mm, Stecksystem: CLASSIC COMBICON, Locking: without, type of packaging: packed in cardboard |  |  | PCB header, nominal cross section: 2.5 mm?, color: green, nominal current: 12 A, rated voltage (III/2): 320 V, contact surface: Gold, type of contact: Male connector, Number of potentials: 2, Number of rows: 1, Number of positions per row: 2, number of connections: 2, product range: MSTBVA 2,5/..-G, pitch: 5.08 mm, mounting: Wave soldering, pin layout: Linear pinning, solder pin [P]: 3.9 mm, Stecksystem: CLASSIC COMBICON, Locking: without, type of packaging: packed in cardboard | 12.15mm | Phoenix Contact | 1747993 |  |  | 651-1747993 | https://www.mouser.co.uk/ProductDetail/Phoenix-Contact/1747993?qs=cq3Rj917t3li0%2FrJTXaRgg%3D%3D
BAT-OUT2 | 1747993 | 1747993 | 1747993 | PCB header, nominal cross section: 2.5 mm?, color: green, nominal current: 12 A, rated voltage (III/2): 320 V, contact surface: Gold, type of contact: Male connector, Number of potentials: 2, Number of rows: 1, Number of positions per row: 2, number of connections: 2, product range: MSTBVA 2,5/..-G, pitch: 5.08 mm, mounting: Wave soldering, pin layout: Linear pinning, solder pin [P]: 3.9 mm, Stecksystem: CLASSIC COMBICON, Locking: without, type of packaging: packed in cardboard |  |  | PCB header, nominal cross section: 2.5 mm?, color: green, nominal current: 12 A, rated voltage (III/2): 320 V, contact surface: Gold, type of contact: Male connector, Number of potentials: 2, Number of rows: 1, Number of positions per row: 2, number of connections: 2, product range: MSTBVA 2,5/..-G, pitch: 5.08 mm, mounting: Wave soldering, pin layout: Linear pinning, solder pin [P]: 3.9 mm, Stecksystem: CLASSIC COMBICON, Locking: without, type of packaging: packed in cardboard | 12.15mm | Phoenix Contact | 1747993 |  |  | 651-1747993 | https://www.mouser.co.uk/ProductDetail/Phoenix-Contact/1747993?qs=cq3Rj917t3li0%2FrJTXaRgg%3D%3D
C1 | 0.1uF | C-EU025-025X050 | C025-025X050 | CAPACITOR, European symbol |  |  |  |  |  |  |  |  |  |  | 65 | C
C2 | 10uF | CPOL-EUE5-10.5 | E5-10,5 | POLARIZED CAPACITOR, European symbol |  |  |  |  |  |  |  |  |  |  | 23 | C
C3 | 0.1uF | C-EU025-030X050 | C025-030X050 | CAPACITOR, European symbol |  |  |  |  |  |  |  |  |  |  | 14 | C
C4 | 0.1uF | C-EU025-030X050 | C025-030X050 | CAPACITOR, European symbol |  |  |  |  |  |  |  |  |  |  | 14 | C
C5 | 0.1uF | C-EU025-030X050 | C025-030X050 | CAPACITOR, European symbol |  |  |  |  |  |  |  |  |  |  | 14 | C
C6 | 0.1uF | C-EU025-030X050 | C025-030X050 | CAPACITOR, European symbol |  |  |  |  |  |  |  |  |  |  | 14 | C
C7 | 10uF | CPOL-EUE5-10.5 | E5-10,5 | POLARIZED CAPACITOR, European symbol |  |  |  |  |  |  |  |  |  |  | 23 | C
C8 | 10uF | CPOL-EUE5-10.5 | E5-10,5 | POLARIZED CAPACITOR, European symbol |  |  |  |  |  |  |  |  |  |  | 23 | C
C9 | 10uF | CPOL-EUE5-10.5 | E5-10,5 | POLARIZED CAPACITOR, European symbol |  |  |  |  |  |  |  |  |  |  | 23 | C
C10 | 10uF | CPOL-EUE5-10.5 | E5-10,5 | POLARIZED CAPACITOR, European symbol |  |  |  |  |  |  |  |  |  |  | 23 | C
H1 | MOUNT-PAD-ROUND3.3 | MOUNT-PAD-ROUND3.3 | 3,3-PAD | MOUNTING PAD, round |  |  |  |  |  |  |  |  |  |  | 1
H2 | MOUNT-PAD-ROUND3.3 | MOUNT-PAD-ROUND3.3 | 3,3-PAD | MOUNTING PAD, round |  |  |  |  |  |  |  |  |  |  | 1
H3 | MOUNT-PAD-ROUND3.3 | MOUNT-PAD-ROUND3.3 | 3,3-PAD | MOUNTING PAD, round |  |  |  |  |  |  |  |  |  |  | 1
H4 | MOUNT-PAD-ROUND3.3 | MOUNT-PAD-ROUND3.3 | 3,3-PAD | MOUNTING PAD, round |  |  |  |  |  |  |  |  |  |  | 1
IC1 | LM1117T-5.0_NOPB | LM1117T-5.0_NOPB | TO254P470X1028X1955-3P | Space saving 800-mA low-dropout linear regulator with internal current limit |  |  | Space saving 800-mA low-dropout linear regulator with internal current limit | 4.7mm | Texas Instruments | LM1117T-5.0/NOPB | 926-LM1117T-50/NOPB | https://www.mouser.com/Search/Refine.aspx?Keyword=926-LM1117T-50%2FNOPB
IC2 | LM1117T-3.3_NOPB | LM1117T-3.3_NOPB | TO254P470X1028X1955-3P | 800mA,3.3V,LDO Voltage Reg.,LM1117T-3.3 Texas Instruments LM1117T-3.3/NOPB, LDO Voltage Regulator, 800mA, 3.3 V |  |  | 800mA,3.3V,LDO Voltage Reg.,LM1117T-3.3 Texas Instruments LM1117T-3.3/NOPB, LDO Voltage Regulator, 800mA, 3.3 V | 4.7mm | Texas Instruments | LM1117T-3.3/NOPB
IC3 | INA219BIDR | INA219BIDR | SOIC127P600X175-8N | 26-V, Bidirectional, Zero-Drift, High-Side, I2C Out Current/Power Monitor |  |  | 26-V, Bidirectional, Zero-Drift, High-Side, I2C Out Current/Power Monitor | 1.75mm | Texas Instruments | INA219BIDR |  |  | 595-INA219BIDR | https://www.mouser.co.uk/ProductDetail/Texas-Instruments/INA219BIDR?qs=1WmUhT%2FVMINyGsXNJcdD5Q%3D%3D
IC4 | INA219BIDR | INA219BIDR | SOIC127P600X175-8N | 26-V, Bidirectional, Zero-Drift, High-Side, I2C Out Current/Power Monitor |  |  | 26-V, Bidirectional, Zero-Drift, High-Side, I2C Out Current/Power Monitor | 1.75mm | Texas Instruments | INA219BIDR |  |  | 595-INA219BIDR | https://www.mouser.co.uk/ProductDetail/Texas-Instruments/INA219BIDR?qs=1WmUhT%2FVMINyGsXNJcdD5Q%3D%3D
IC5 | INA219BIDR | INA219BIDR | SOIC127P600X175-8N | 26-V, Bidirectional, Zero-Drift, High-Side, I2C Out Current/Power Monitor |  |  | 26-V, Bidirectional, Zero-Drift, High-Side, I2C Out Current/Power Monitor | 1.75mm | Texas Instruments | INA219BIDR |  |  | 595-INA219BIDR | https://www.mouser.co.uk/ProductDetail/Texas-Instruments/INA219BIDR?qs=1WmUhT%2FVMINyGsXNJcdD5Q%3D%3D
JST-XH1 | I2C-BUS | JST-XH-05-PIN-LONG-PAD | JST-XH-05-PACKAGE-LONG-PAD | JST XH Connector 2 Pin
JST-XH2 | I2C-BUS | JST-XH-05-PIN-LONG-PAD | JST-XH-05-PACKAGE-LONG-PAD | JST XH Connector 2 Pin
JST-XH3 | BAT-BALANCE | JST-XH-04-PIN-LONG-PAD | JST-XH-04-PACKAGE-LONG-PAD | JST XH Connector 2 Pin
PWR-3V3 | GN | LED5MM | LED5MM | LED
PWR-5V | GN | LED5MM | LED5MM | LED
R1 | 12m | R-EU_0204/7 | 0204/7 | RESISTOR, European symbol |  |  |  |  |  |  |  |  |  |  | 79 | R
R2 | tbd | R-EU_0204/7 | 0204/7 | RESISTOR, European symbol |  |  |  |  |  |  |  |  |  |  | 79 | R
R3 | tbd | R-EU_0204/7 | 0204/7 | RESISTOR, European symbol |  |  |  |  |  |  |  |  |  |  | 79 | R
R4 | 10k | R-EU_0204/7 | 0204/7 | RESISTOR, European symbol |  |  |  |  |  |  |  |  |  |  | 79 | R
R5 | 220 | R-EU_0204/7 | 0204/7 | RESISTOR, European symbol |  |  |  |  |  |  |  |  |  |  | 79 | R
R6 | 220 | R-EU_0204/7 | 0204/7 | RESISTOR, European symbol |  |  |  |  |  |  |  |  |  |  | 79 | R
R7 | 220 | R-EU_0204/7 | 0204/7 | RESISTOR, European symbol |  |  |  |  |  |  |  |  |  |  | 79 | R
RESET |  | SWITCH_PUSHBUTTONEVQ-PE | TACT_PANA-EVQ | Buttons
STATUS | RD | LED5MM | LED5MM | LED
U$1 | ATTINY84DIP | ATTINY84DIP | ATTINY84(DIP)

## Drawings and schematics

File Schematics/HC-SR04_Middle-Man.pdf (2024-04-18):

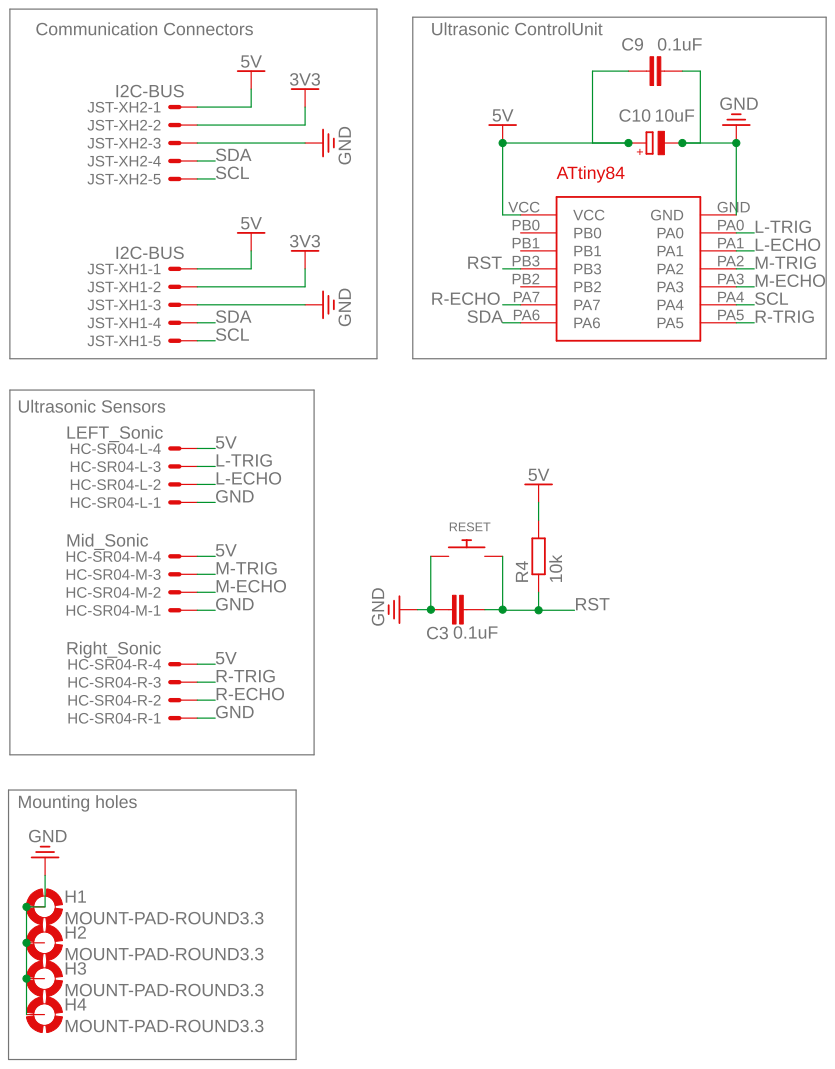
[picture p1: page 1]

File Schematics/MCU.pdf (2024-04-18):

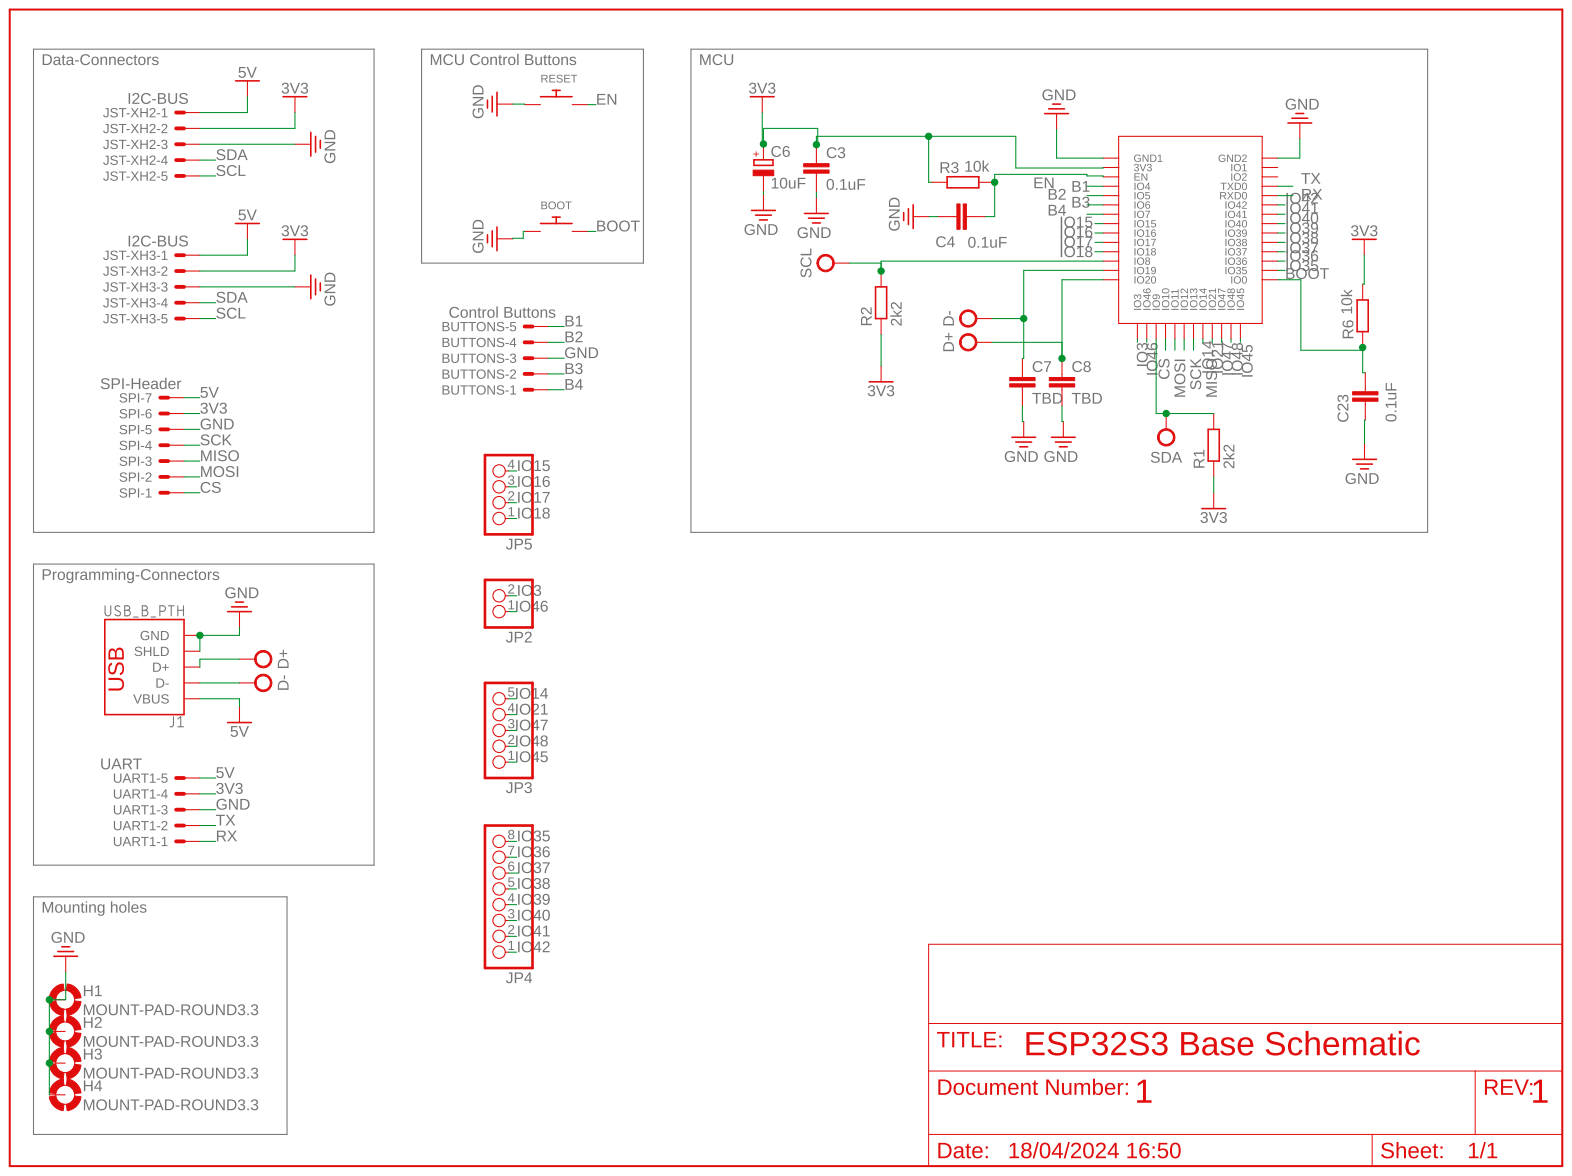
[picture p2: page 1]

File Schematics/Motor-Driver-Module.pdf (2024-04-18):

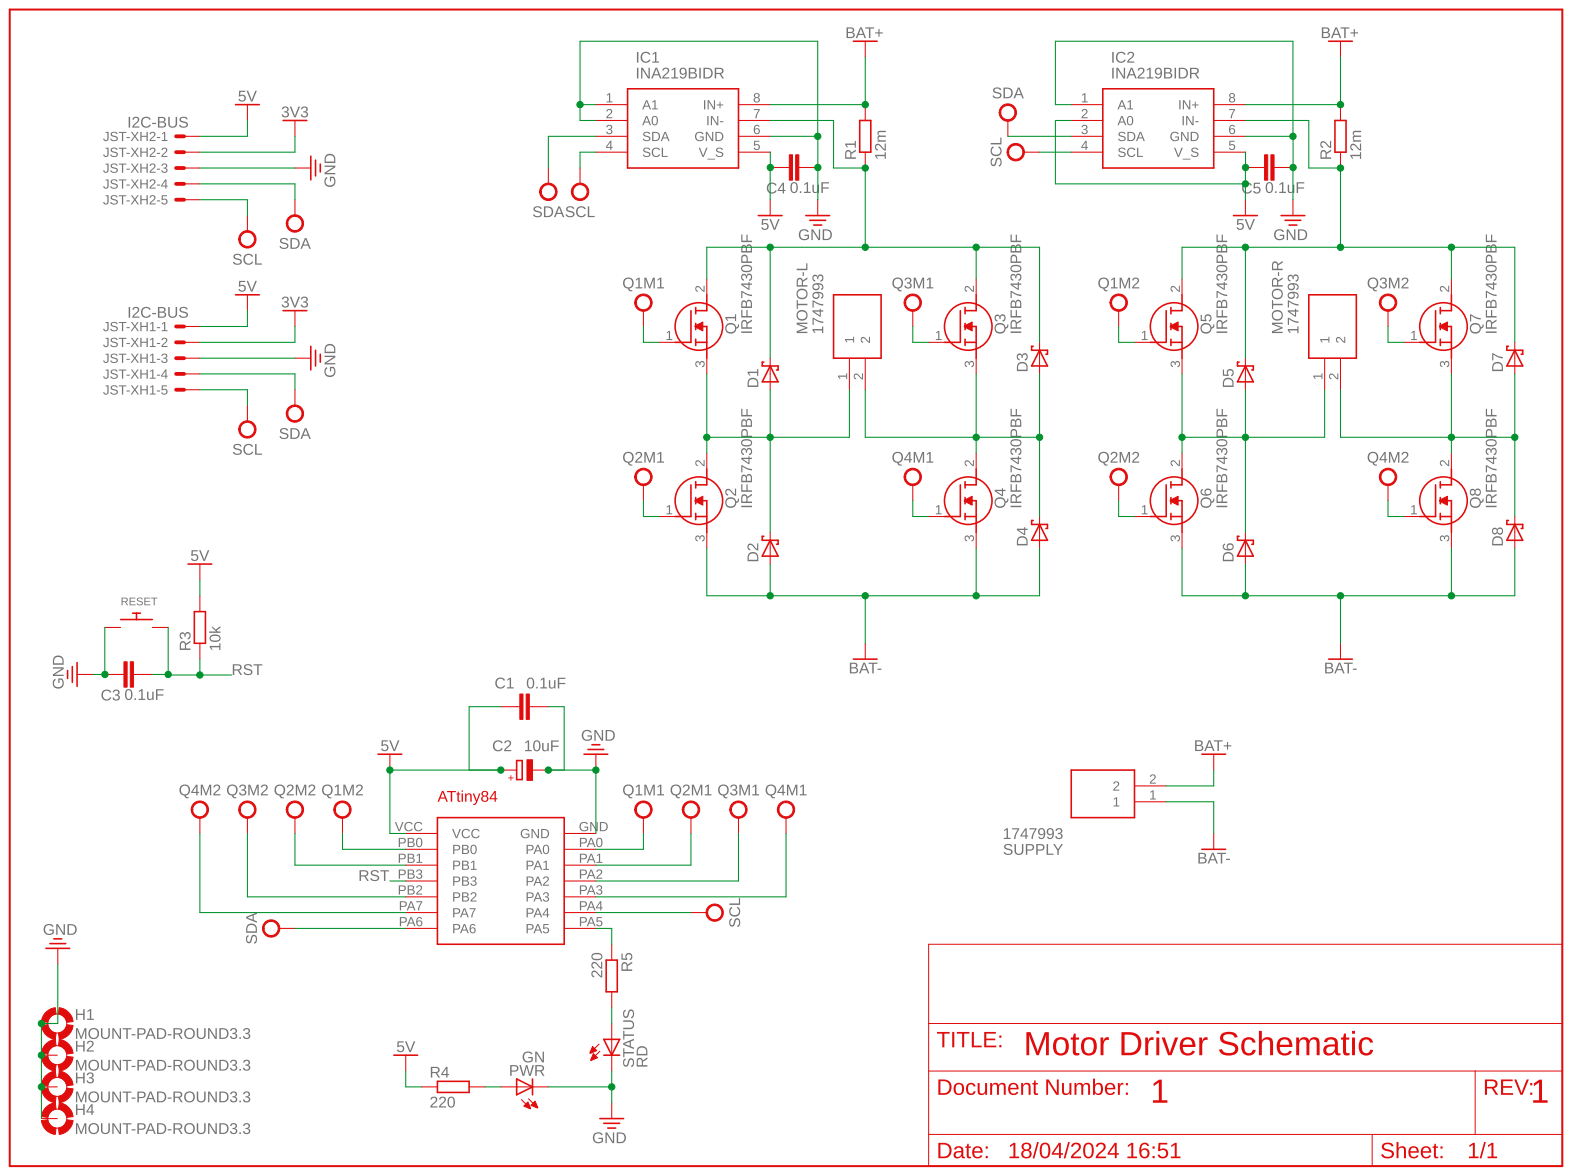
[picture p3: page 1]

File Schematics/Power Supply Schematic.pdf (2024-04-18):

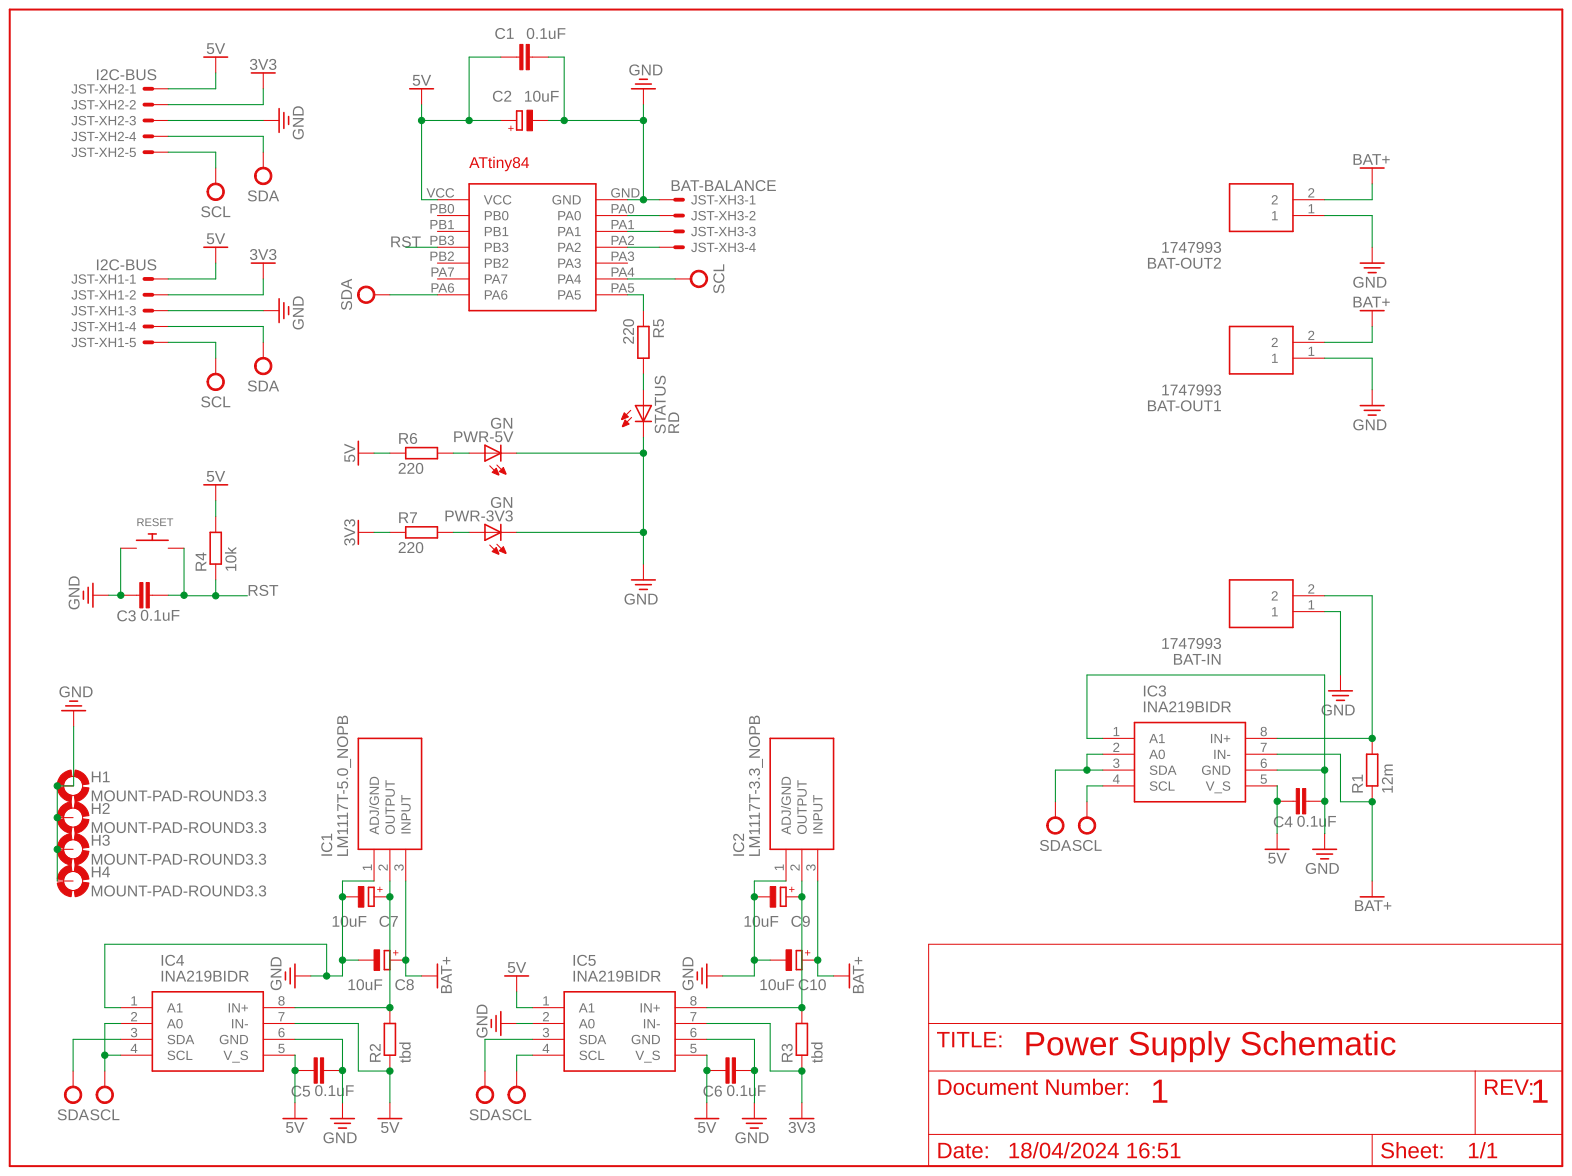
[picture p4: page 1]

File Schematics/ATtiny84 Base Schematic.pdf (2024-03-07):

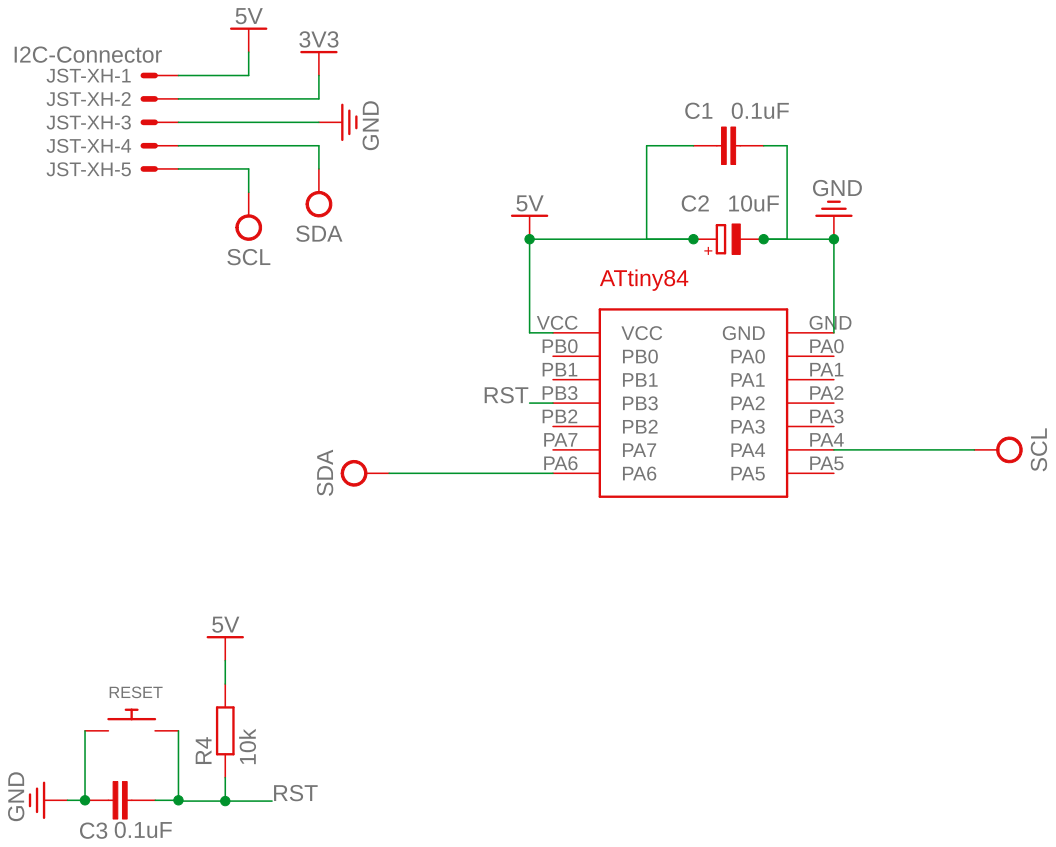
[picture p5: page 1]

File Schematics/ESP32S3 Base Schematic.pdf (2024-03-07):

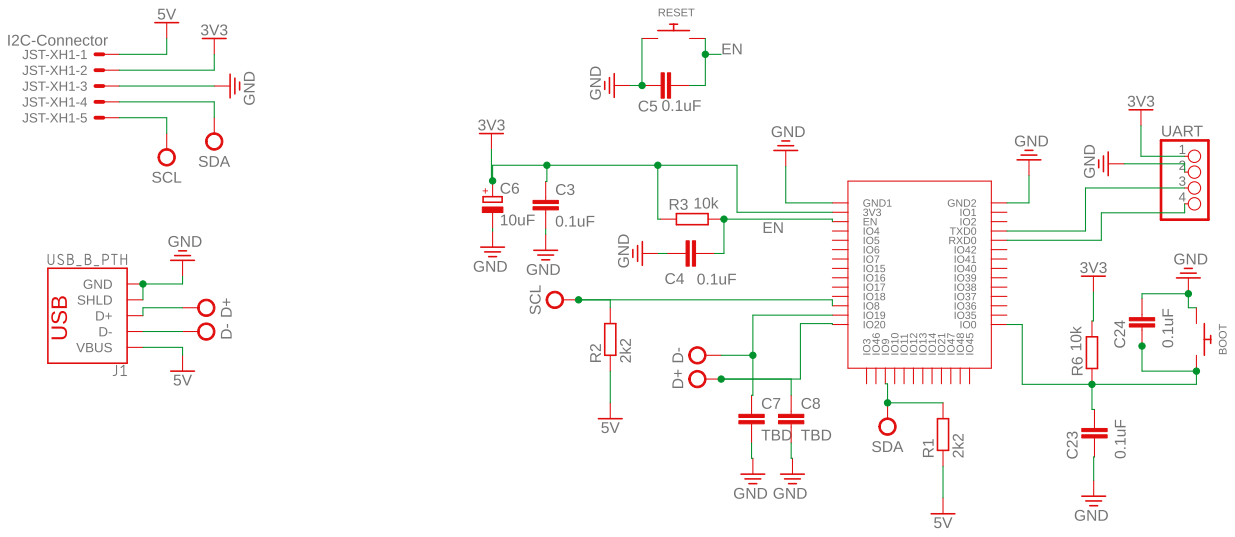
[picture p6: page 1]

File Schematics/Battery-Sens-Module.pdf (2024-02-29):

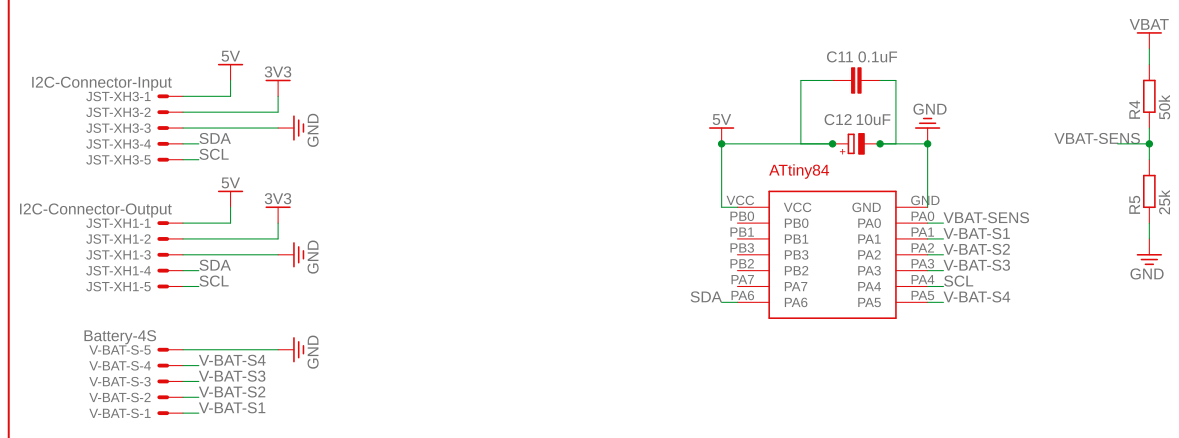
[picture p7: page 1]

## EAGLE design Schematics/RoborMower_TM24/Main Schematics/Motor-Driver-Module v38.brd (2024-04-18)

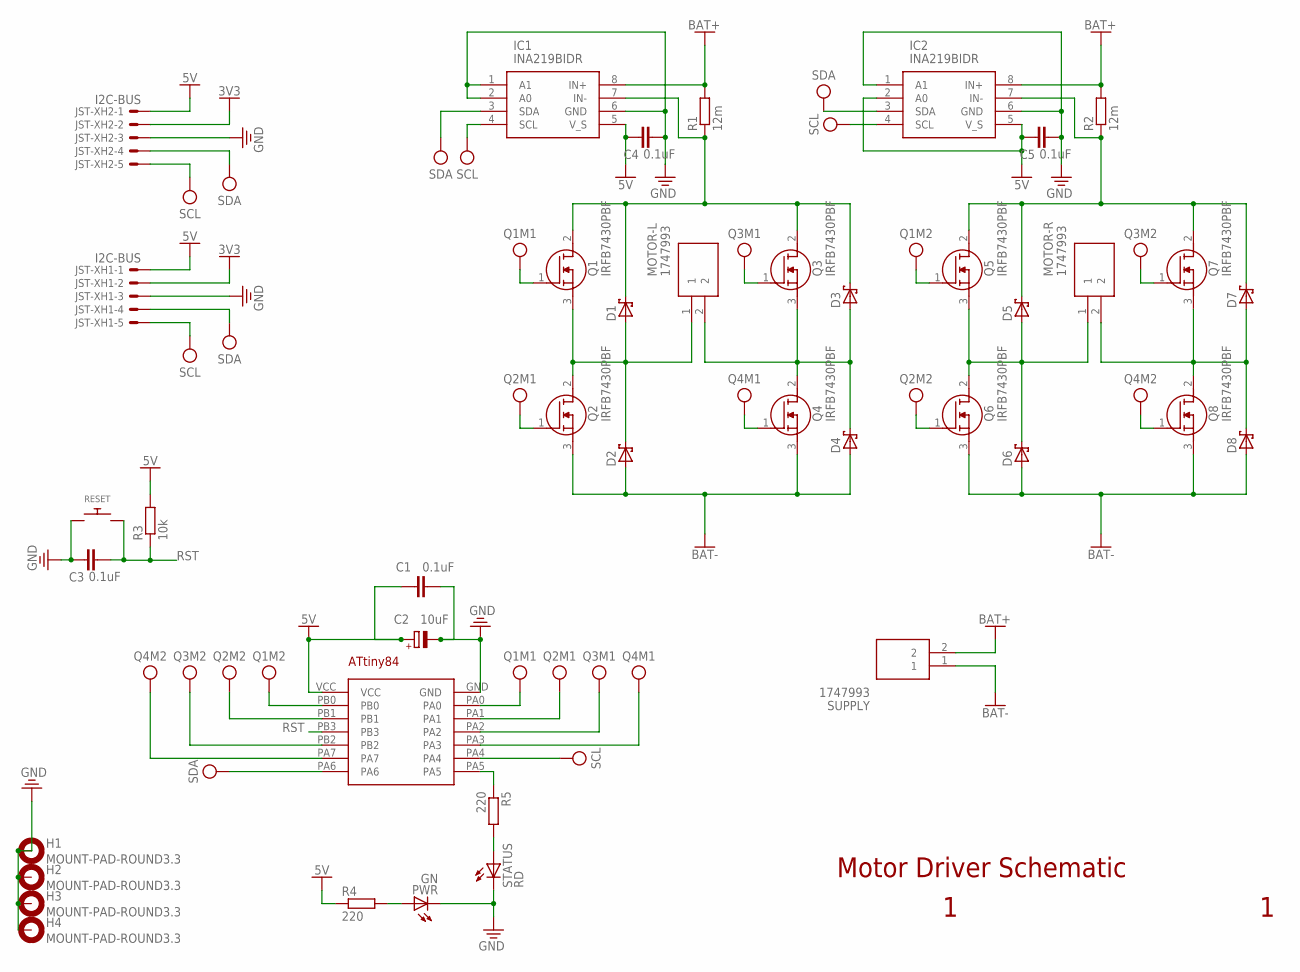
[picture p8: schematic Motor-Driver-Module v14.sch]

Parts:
C1: 0.1uF; C025-025X050
C2: 10uF; E5-10,5
C3, C4, C5: 0.1uF; C025-030X050
D1, D2, D3, D4, D5, D6, D7, D8: SCHOTTKY-DIODEDO41; DO41-10
H1, H2, H3, H4: MOUNT-PAD-ROUND3.3; 3,3-PAD
IC1, IC2: INA219BIDR; SOIC127P600X175-8N
JST-XH1, JST-XH2: I2C-BUS; JST-XH-05-PACKAGE-LONG-PAD
MOTOR-L: 1747993
MOTOR-R: 1747993
PWR: GN; LED5MM
Q1, Q2, Q3, Q4, Q5, Q6, Q7, Q8: IRFB7430PBF; TO254P483X1016X1994-3P
R1, R2: 12m; 0204/7
R3: 10k; 0204/7
R4, R5: 220; 0204/7
RESET: SWITCH_PUSHBUTTONEVQ-PE; TACT_PANA-EVQ
STATUS: RD; LED5MM
SUPPLY: 1747993
U$1: ATTINY84DIP; ATTINY84(DIP)

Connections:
3V3: JST-XH1.2, JST-XH2.2
5V: C1.1, C2.+, C4.1, C5.1, IC1.5 (V_S), IC2.2 (A0), IC2.5 (V_S), JST-XH1.1, JST-XH2.1, R3.2, R4.1, U$1.VCC
BAT+: IC1.8 (IN+), IC2.8 (IN+), R1.2, R2.2, SUPPLY.2
BAT-: D2.A, D4.A, D6.A, D8.A, Q2.3 (S), Q4.3 (S), Q6.3 (S), Q8.3 (S), SUPPLY.1
GND: C1.2, C2.-, C3.1, C4.2, C5.2, H1.B3,3, H2.B3,3, H3.B3,3, H4.B3,3, IC1.1 (A1), IC1.2 (A0), IC1.6 (GND), IC2.1 (A1), IC2.6 (GND), JST-XH1.3, JST-XH2.3, PWR.K (C), RESET.P$1, STATUS.K (C), U$1.GND
unnamed: D3.A, D4.C, MOTOR-L.2, Q3.3 (S), Q4.2 (D)
unnamed: D1.A, D2.C, MOTOR-L.1, Q1.3 (S), Q2.2 (D)
unnamed: D7.A, D8.C, MOTOR-R.2, Q7.3 (S), Q8.2 (D)
unnamed: D5.A, D6.C, MOTOR-R.1, Q5.3 (S), Q6.2 (D)
unnamed: D1.C, D3.C, IC1.7 (IN-), Q1.2 (D), Q3.2 (D), R1.1
unnamed: D5.C, D7.C, IC2.7 (IN-), Q5.2 (D), Q7.2 (D), R2.1
unnamed: R5.1, U$1.PA5
unnamed: R5.2, STATUS.A
unnamed: PWR.A, R4.2
Q1M1: Q1.1 (G), U$1.PA0
Q1M2: Q5.1 (G), U$1.PB0
Q2M1: Q2.1 (G), U$1.PA1
Q2M2: Q6.1 (G), U$1.PB1
Q3M1: Q3.1 (G), U$1.PA2
Q3M2: Q7.1 (G), U$1.PB2
Q4M1: Q4.1 (G), U$1.PA3
Q4M2: Q8.1 (G), U$1.PA7
RST: C3.2, R3.1, RESET.P$2, U$1.PB3
SCL: IC1.4 (SCL), IC2.4 (SCL), JST-XH1.5, JST-XH2.5, U$1.PA4
SDA: IC1.3 (SDA), IC2.3 (SDA), JST-XH1.4, JST-XH2.4, U$1.PA6

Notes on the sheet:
Motor Driver Schematic

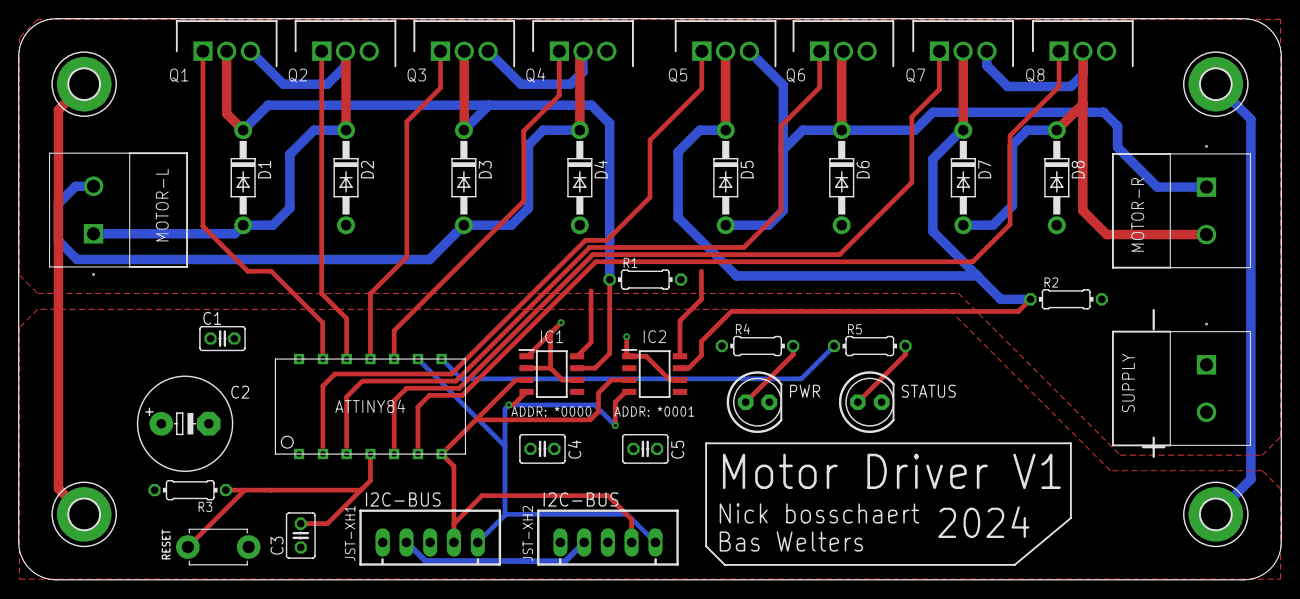
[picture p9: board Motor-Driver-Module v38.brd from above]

Board: 2 copper layers, 135.0 x 60.0 mm, 41 parts (0 on the bottom side), 25 nets.

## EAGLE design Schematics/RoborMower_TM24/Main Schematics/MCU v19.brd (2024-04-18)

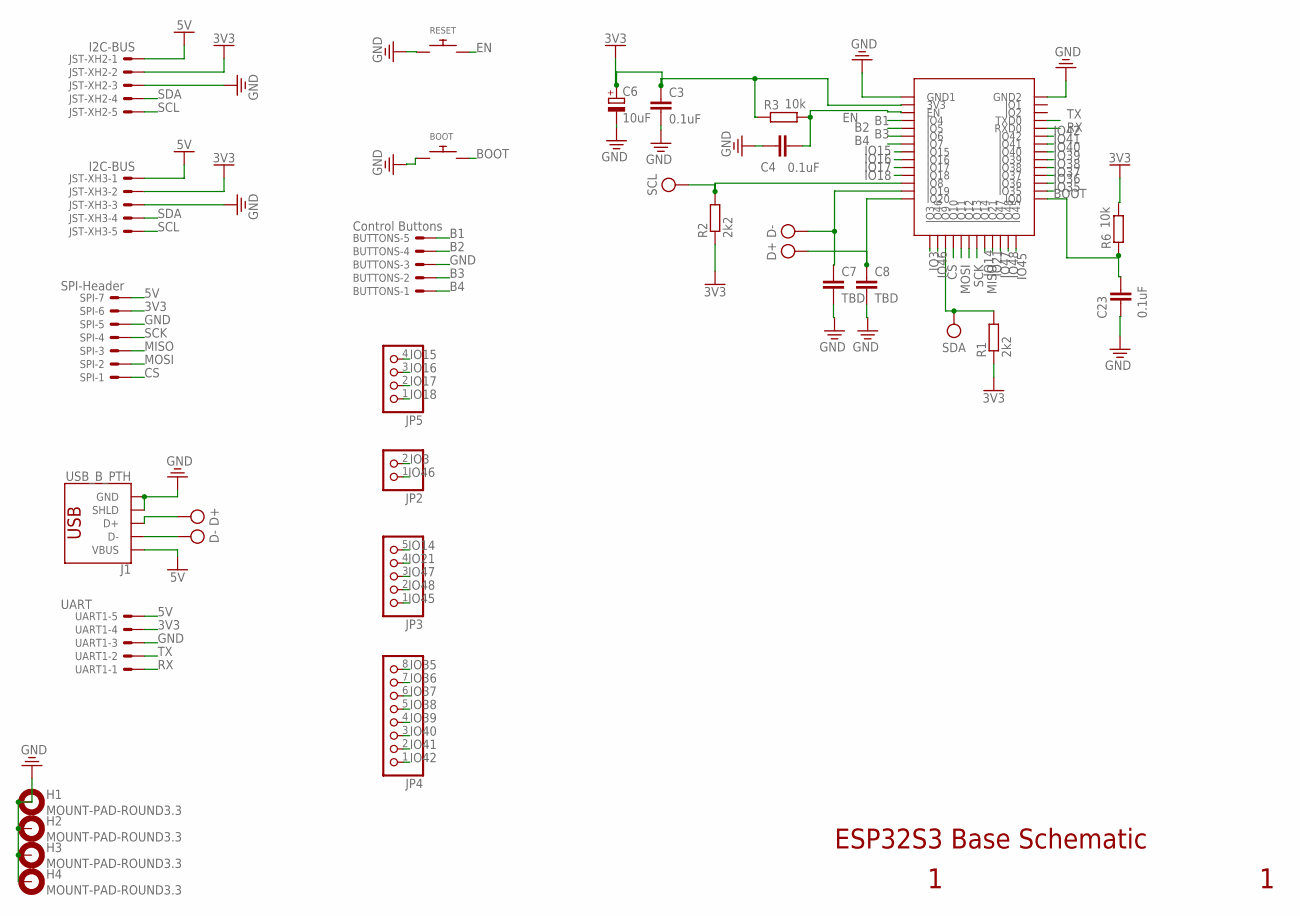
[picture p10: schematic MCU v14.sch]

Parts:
BOOT: SWITCH_PUSHBUTTONEVQ-PE; TACT_PANA-EVQ
BUTTONS: Control Buttons; JST-XH-05-PACKAGE-LONG-PAD
C3, C4, C23: 0.1uF; C025-030X050
C6: 10uF; CAPPRD508W65D1000H1100B
C7, C8: TBD; C025-030X050
H1, H2, H3, H4: MOUNT-PAD-ROUND3.3; 3,3-PAD
J1: USB_B_PTH; USB-B-PTH
JP2: PINHD-1X2; 1X02
JP3: PINHD-1X55X2MM; 1_05X2MM
JP4: PINHD-1X8; 1X08
JP5: PINHD-1X4; 1X04
JST-XH2, JST-XH3: I2C-BUS; JST-XH-05-PACKAGE-LONG-PAD
R1, R2: 2k2; 0204/5
R3, R6: 10k; 0204/7
RESET: SWITCH_PUSHBUTTONEVQ-PE; TACT_PANA-EVQ
SPI: SPI-Header; JST-XH-07-PACKAGE-LONG-PAD
U$1: ESP32-S3-WROOM-1
UART1: UART; JST-XH-05-PACKAGE-ROUND-PAD

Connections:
3V3: C3.1, C6.1 (+), JST-XH2.2, JST-XH3.2, R1.1, R2.1, R3.1, R6.2, SPI.6, U$1.3V3, UART1.4
5V: J1.VBUS, JST-XH2.1, JST-XH3.1, SPI.7, UART1.5
B1: BUTTONS.5, U$1.IO4
B2: BUTTONS.4, U$1.IO5
B3: BUTTONS.2, U$1.IO6
B4: BUTTONS.1, U$1.IO7
BOOT: BOOT.P$2, C23.2, R6.1, U$1.IO0
CS: SPI.1, U$1.IO10
D+: C8.1, J1.D+, U$1.IO20
D-: C7.1, J1.D-, U$1.IO19
EN: C4.2, R3.2, RESET.P$2, U$1.EN
GND: BOOT.P$1, BUTTONS.3, C3.2, C4.1, C6.2 (-), C7.2, C8.2, C23.1, H1.B3,3, H2.B3,3, H3.B3,3, H4.B3,3, J1.GND, J1.SHLD1 (SHLD), J1.SHLD2 (SHLD), JST-XH2.3, JST-XH3.3, RESET.P$1, SPI.5, U$1.GND1, U$1.GND2, UART1.3
IO3: JP2.2, U$1.IO3
IO14: JP3.5, U$1.IO14
IO15: JP5.4, U$1.IO15
IO16: JP5.3, U$1.IO16
IO17: JP5.2, U$1.IO17
IO18: JP5.1, U$1.IO18
IO21: JP3.4, U$1.IO21
IO35: JP4.8, U$1.IO35
IO36: JP4.7, U$1.IO36
IO37: JP4.6, U$1.IO37
IO38: JP4.5, U$1.IO38
IO39: JP4.4, U$1.IO39
IO40: JP4.3, U$1.IO40
IO41: JP4.2, U$1.IO41
IO42: JP4.1, U$1.IO42
IO45: JP3.1, U$1.IO45
IO46: JP2.1, U$1.IO46
IO47: JP3.3, U$1.IO47
IO48: JP3.2, U$1.IO48
MISO: SPI.3, U$1.IO13
MOSI: SPI.2, U$1.IO11
RX: U$1.RXD0, UART1.1
SCK: SPI.4, U$1.IO12
SCL: JST-XH2.5, JST-XH3.5, R2.2, U$1.IO8
SDA: JST-XH2.4, JST-XH3.4, R1.2, U$1.IO9
TX: U$1.TXD0, UART1.2

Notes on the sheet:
ESP32S3 Base Schematic

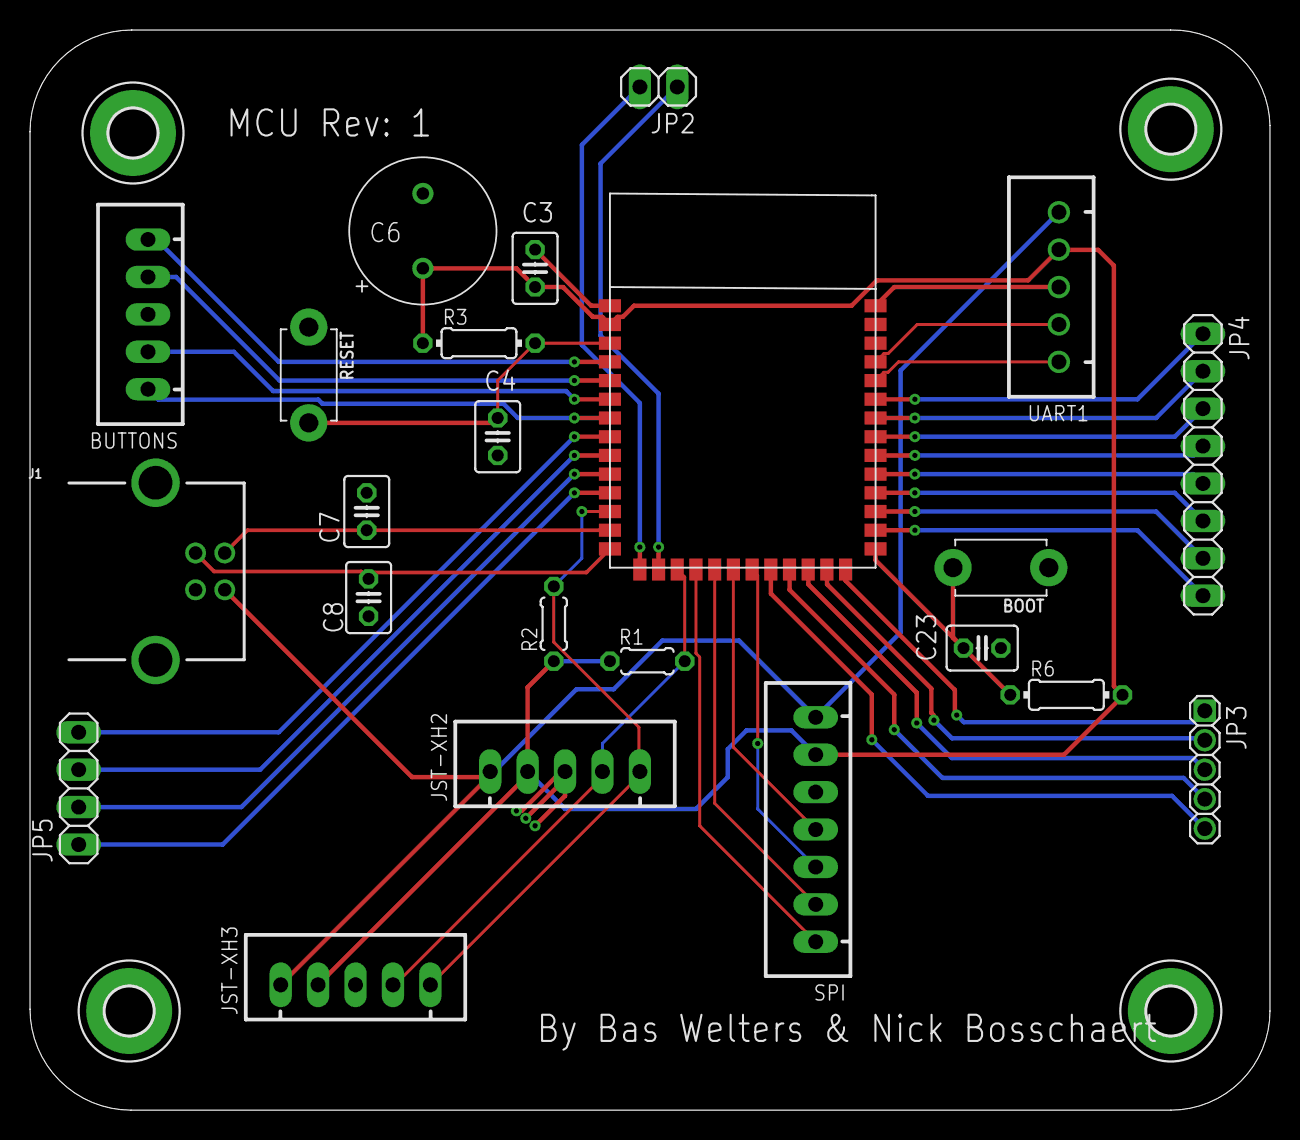
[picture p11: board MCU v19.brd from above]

Board: 2 copper layers, 84.2 x 73.3 mm, 27 parts (0 on the bottom side), 38 nets.

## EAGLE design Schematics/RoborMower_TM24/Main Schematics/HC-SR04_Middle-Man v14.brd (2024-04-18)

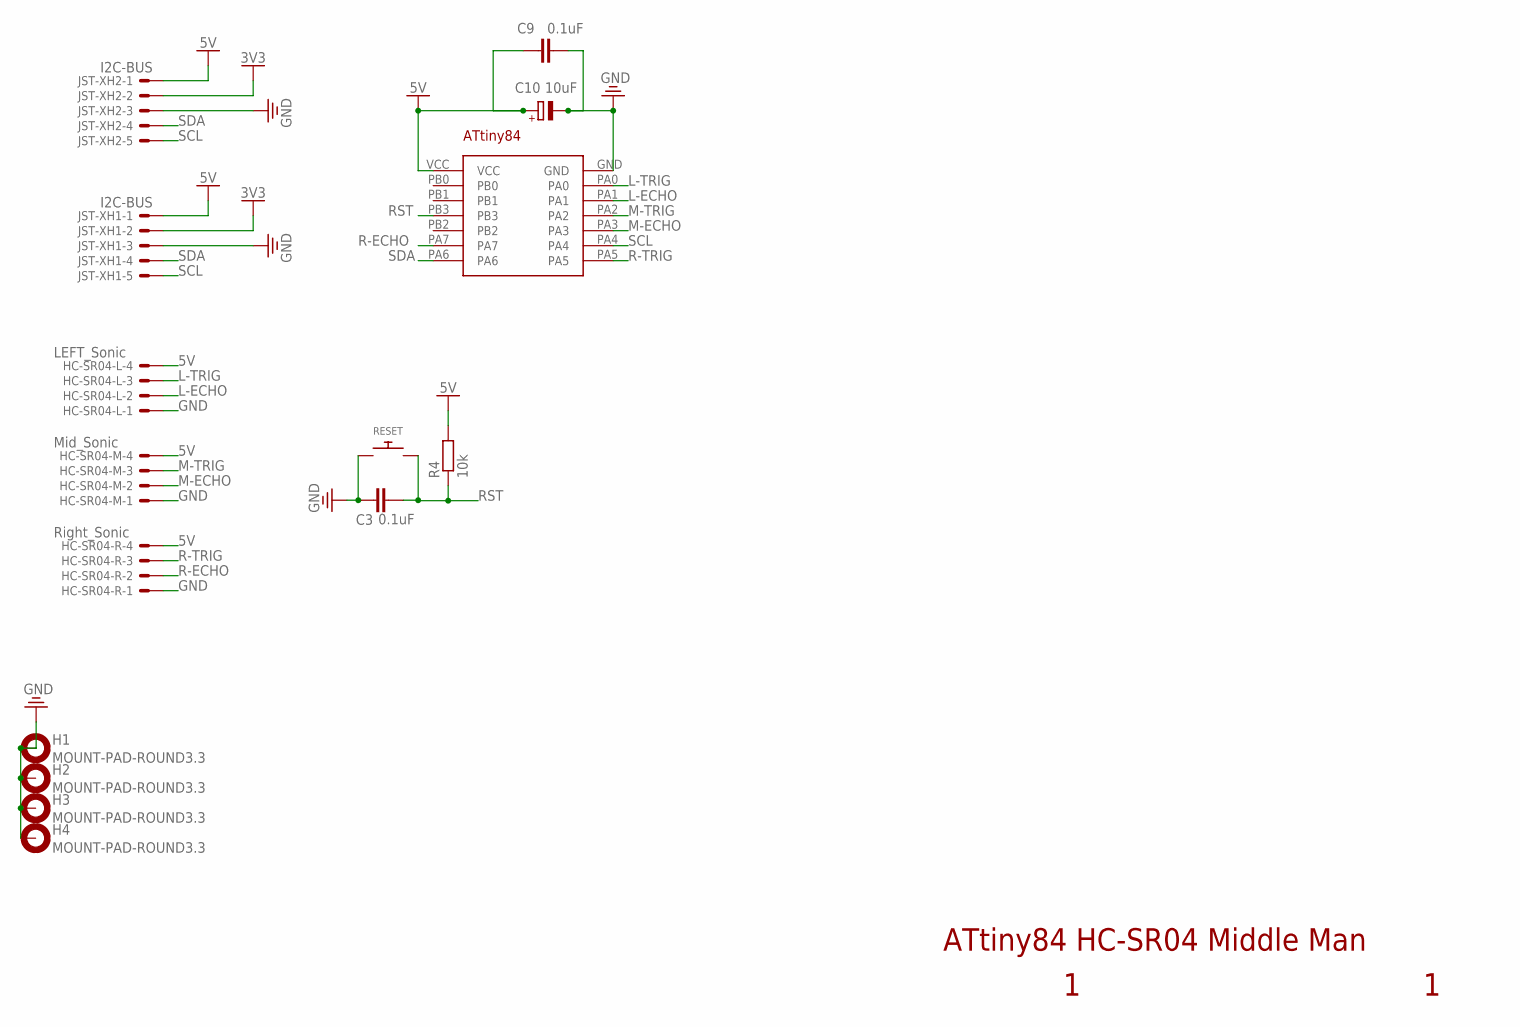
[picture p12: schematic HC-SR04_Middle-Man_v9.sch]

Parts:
C3: 0.1uF; C025-030X050
C9: 0.1uF; C025-025X050
C10: 10uF; E5-10,5
H1, H2, H3, H4: MOUNT-PAD-ROUND3.3; 3,3-PAD
HC-SR04-L: LEFT_Sonic; JST-XH-04-PACKAGE-LONG-PAD
HC-SR04-M: Mid_Sonic; JST-XH-04-PACKAGE-LONG-PAD
HC-SR04-R: Right_Sonic; JST-XH-04-PACKAGE-LONG-PAD
JST-XH1, JST-XH2: I2C-BUS; JST-XH-05-PACKAGE-LONG-PAD
R4: 10k; 0204/7
RESET: SWITCH_PUSHBUTTONEVQ-PE; TACT_PANA-EVQ
U$3: ATTINY84DIP; ATTINY84(DIP)

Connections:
3V3: JST-XH1.2, JST-XH2.2
5V: C9.1, C10.+, HC-SR04-L.4, HC-SR04-M.4, HC-SR04-R.4, JST-XH1.1, JST-XH2.1, R4.2, U$3.VCC
GND: C3.1, C9.2, C10.-, H1.B3,3, H2.B3,3, H3.B3,3, H4.B3,3, HC-SR04-L.1, HC-SR04-M.1, HC-SR04-R.1, JST-XH1.3, JST-XH2.3, RESET.P$1, U$3.GND
L-ECHO: HC-SR04-L.2, U$3.PA1
L-TRIG: HC-SR04-L.3, U$3.PA0
M-ECHO: HC-SR04-M.2, U$3.PA3
M-TRIG: HC-SR04-M.3, U$3.PA2
R-ECHO: HC-SR04-R.2, U$3.PA7
R-TRIG: HC-SR04-R.3, U$3.PA5
RST: C3.2, R4.1, RESET.P$2, U$3.PB3
SCL: JST-XH1.5, JST-XH2.5, U$3.PA4
SDA: JST-XH1.4, JST-XH2.4, U$3.PA6

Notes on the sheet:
ATtiny84 HC-SR04 Middle Man

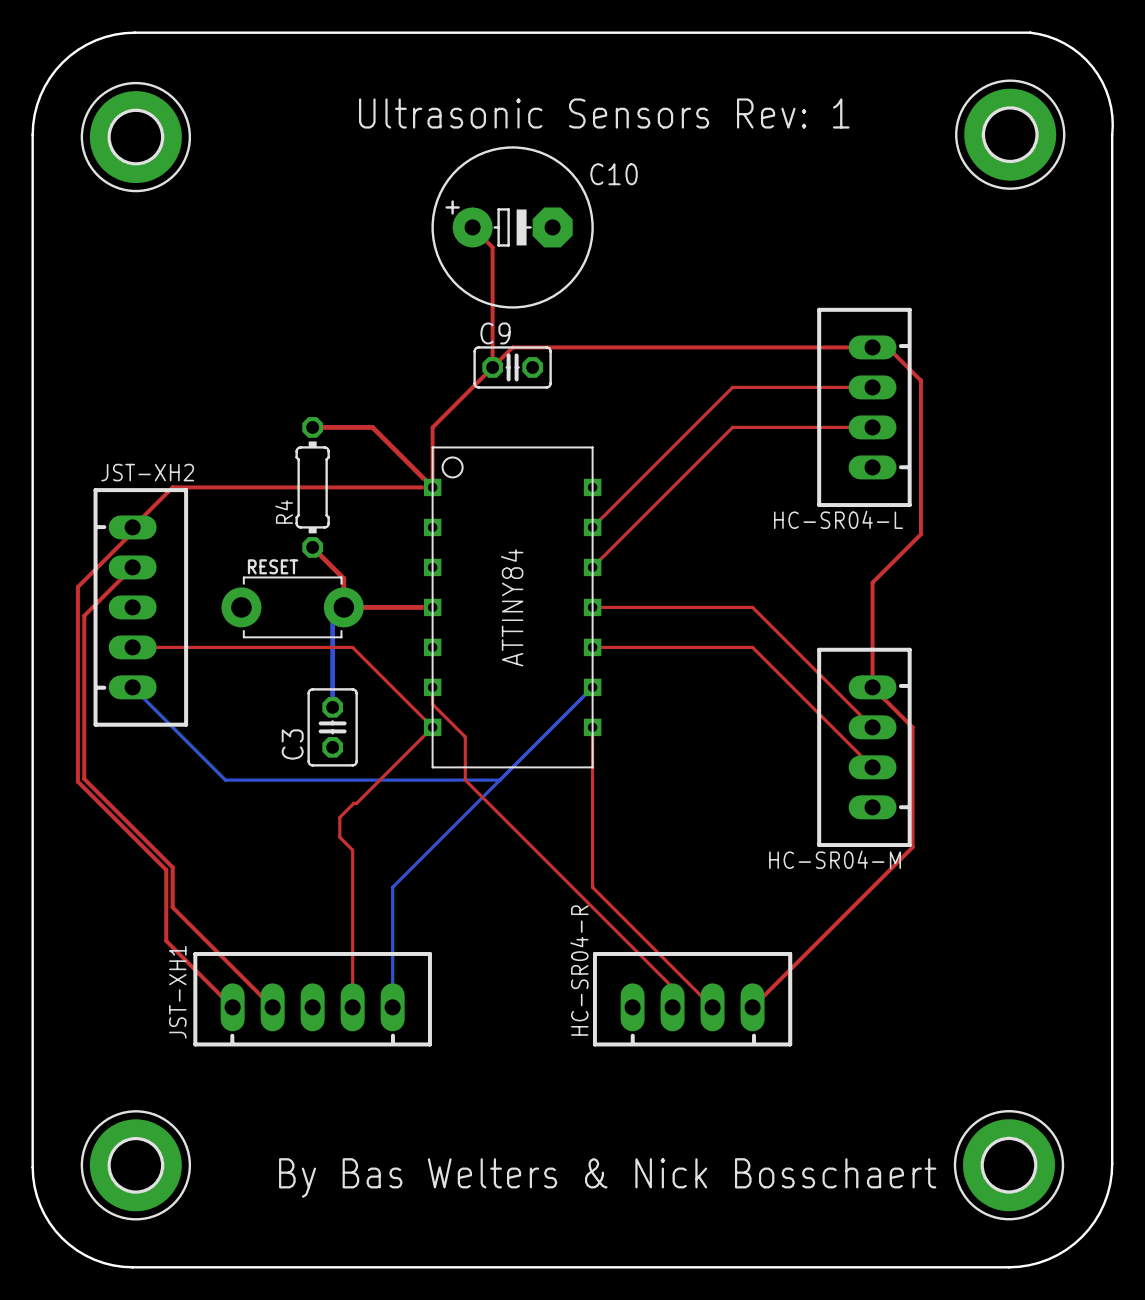
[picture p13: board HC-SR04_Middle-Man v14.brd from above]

Board: 2 copper layers, 68.6 x 78.4 mm, 15 parts (0 on the bottom side), 12 nets.

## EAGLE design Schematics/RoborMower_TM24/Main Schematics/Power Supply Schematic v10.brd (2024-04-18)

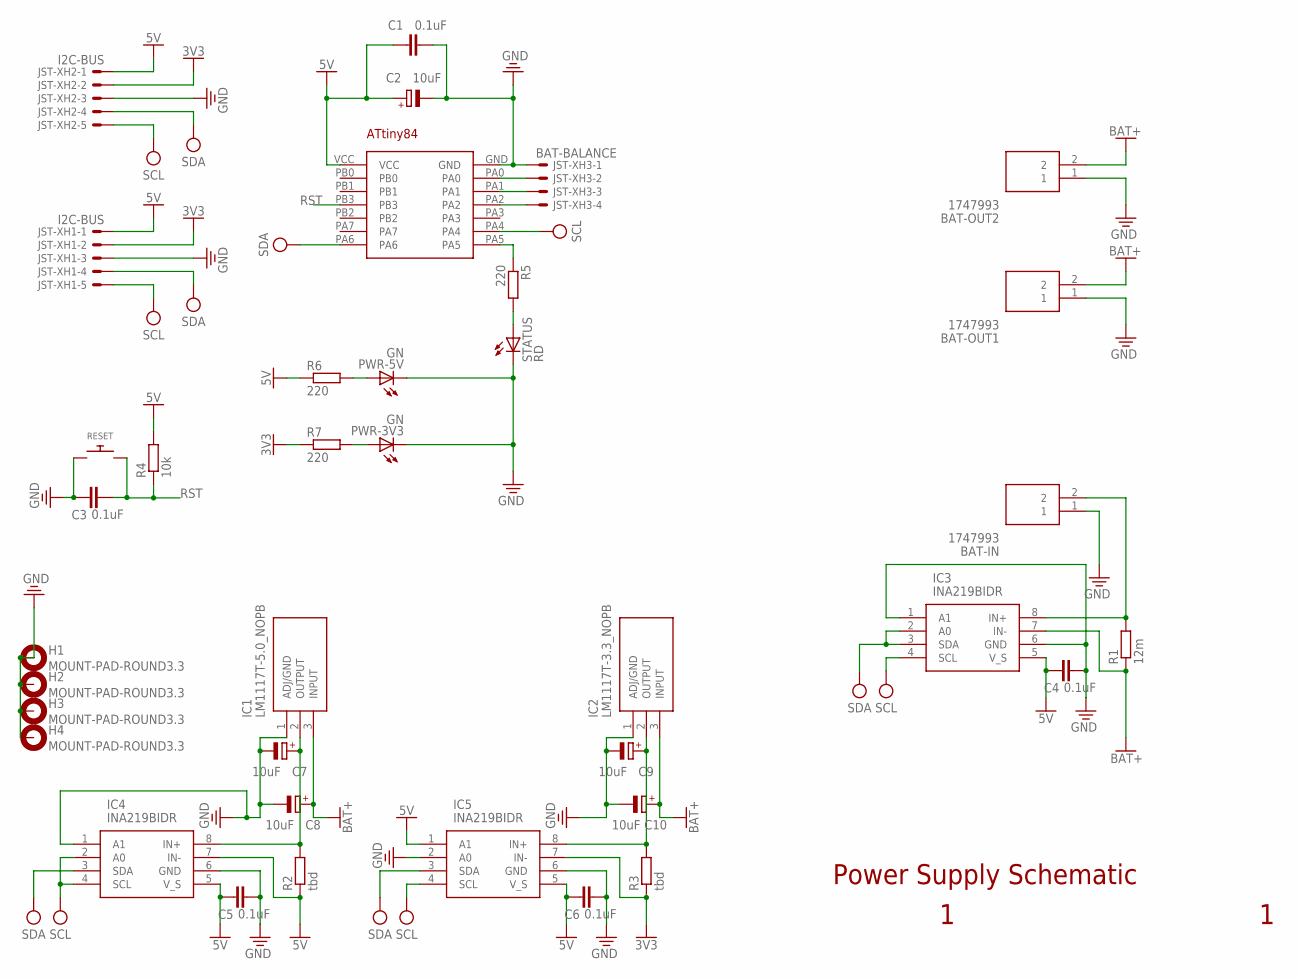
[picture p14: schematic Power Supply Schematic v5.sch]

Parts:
BAT-IN: 1747993
BAT-OUT1, BAT-OUT2: 1747993
C1: 0.1uF; C025-025X050
C2, C7, C8, C9, C10: 10uF; E5-10,5
C3, C4, C5, C6: 0.1uF; C025-030X050
H1, H2, H3, H4: MOUNT-PAD-ROUND3.3; 3,3-PAD
IC1: LM1117T-5.0_NOPB; TO254P470X1028X1955-3P
IC2: LM1117T-3.3_NOPB; TO254P470X1028X1955-3P
IC3, IC4, IC5: INA219BIDR; SOIC127P600X175-8N
JST-XH1, JST-XH2: I2C-BUS; JST-XH-05-PACKAGE-LONG-PAD
JST-XH3: BAT-BALANCE; JST-XH-04-PACKAGE-LONG-PAD
PWR-3V3, PWR-5V: GN; LED5MM
R1: 12m; 0204/7
R2, R3: tbd; 0204/7
R4: 10k; 0204/7
R5, R6, R7: 220; 0204/7
RESET: SWITCH_PUSHBUTTONEVQ-PE; TACT_PANA-EVQ
STATUS: RD; LED5MM
U$1: ATTINY84DIP; ATTINY84(DIP)

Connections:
3V3: IC5.7 (IN-), JST-XH1.2, JST-XH2.2, R3.1, R7.1
5V: C1.1, C2.+, C4.1, C5.1, C6.1, IC3.5 (V_S), IC4.5 (V_S), IC4.7 (IN-), IC5.1 (A1), IC5.5 (V_S), JST-XH1.1, JST-XH2.1, R2.1, R4.2, R6.1, U$1.VCC
BAT+: BAT-OUT1.2, BAT-OUT2.2, C8.+, C10.+, IC1.3 (INPUT), IC2.3 (INPUT), IC3.7 (IN-), R1.1
GND: BAT-IN.1, BAT-OUT1.1, BAT-OUT2.1, C1.2, C2.-, C3.1, C4.2, C5.2, C6.2, C7.-, C8.-, C9.-, C10.-, H1.B3,3, H2.B3,3, H3.B3,3, H4.B3,3, IC1.1 (ADJ/GND), IC2.1 (ADJ/GND), IC3.1 (A1), IC3.6 (GND), IC4.1 (A1), IC4.6 (GND), IC5.2 (A0), IC5.6 (GND), JST-XH1.3, JST-XH2.3, JST-XH3.1, PWR-3V3.K (C), PWR-5V.K (C), RESET.P$1, STATUS.K (C), U$1.GND
unnamed: BAT-IN.2, IC3.8 (IN+), R1.2
unnamed: JST-XH3.2, U$1.PA0
unnamed: JST-XH3.3, U$1.PA1
unnamed: JST-XH3.4, U$1.PA2
unnamed: C7.+, IC1.2 (OUTPUT), IC4.8 (IN+), R2.2
unnamed: C9.+, IC2.2 (OUTPUT), IC5.8 (IN+), R3.2
unnamed: R5.1, U$1.PA5
unnamed: R5.2, STATUS.A
unnamed: PWR-5V.A, R6.2
unnamed: PWR-3V3.A, R7.2
RST: C3.2, R4.1, RESET.P$2, U$1.PB3
SCL: IC3.4 (SCL), IC4.2 (A0), IC4.4 (SCL), IC5.4 (SCL), JST-XH1.5, JST-XH2.5, U$1.PA4
SDA: IC3.2 (A0), IC3.3 (SDA), IC4.3 (SDA), IC5.3 (SDA), JST-XH1.4, JST-XH2.4, U$1.PA6

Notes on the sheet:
Power Supply Schematic

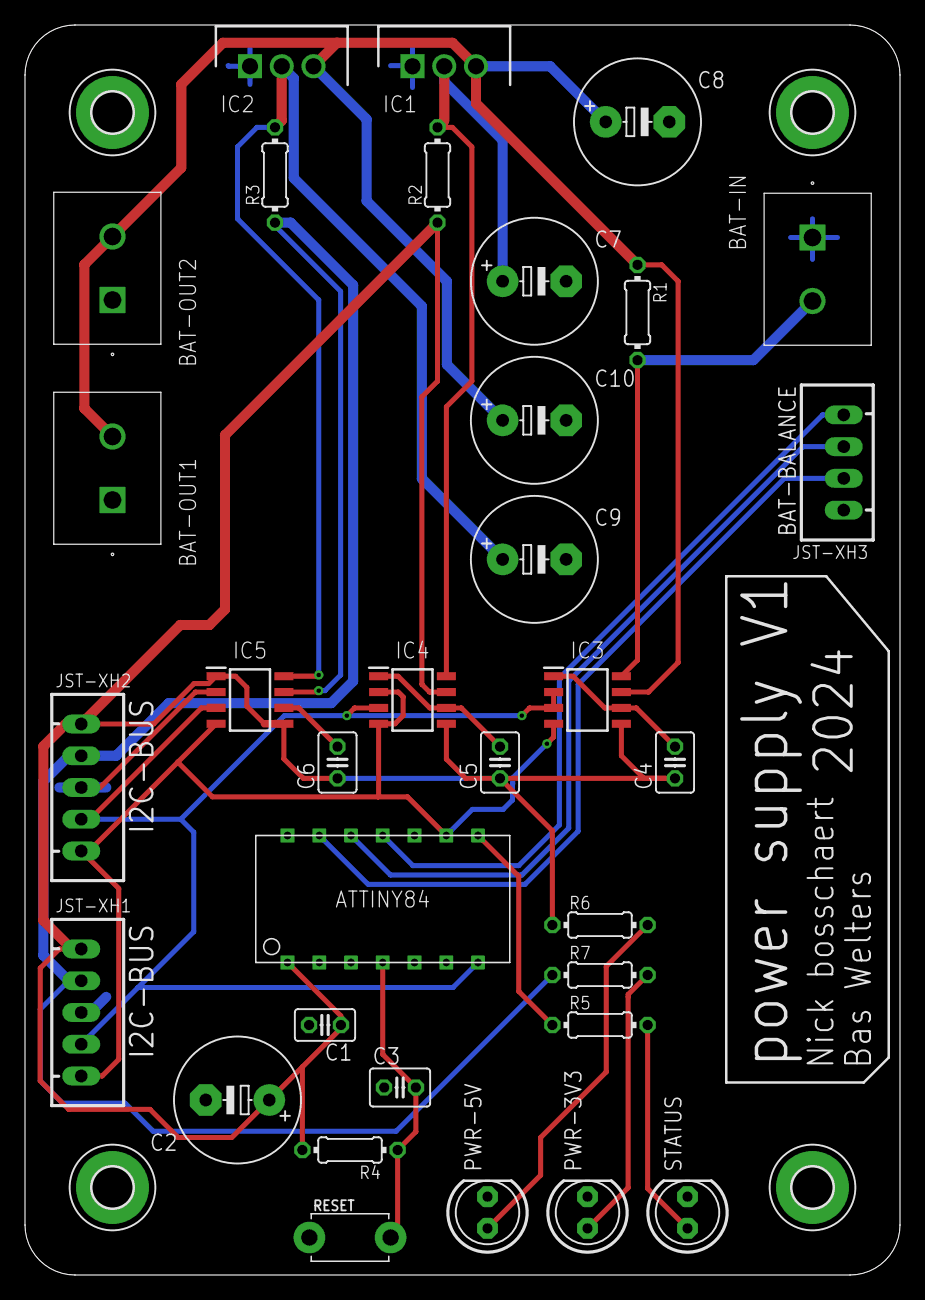
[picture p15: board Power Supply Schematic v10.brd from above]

Board: 2 copper layers, 70.0 x 100.0 mm, 37 parts (0 on the bottom side), 17 nets.

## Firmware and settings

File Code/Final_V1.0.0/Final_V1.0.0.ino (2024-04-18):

String leftValue;
String middleValue;
String rightValue;

bool testFlag = false;

int currentMillis = 0;
int lastObjectMillis = 0;

#define delayMS 500

#include <Wire.h>

float currentSensorReading[3][4];

#include "INA219Driver.h"

#include <LiquidCrystal_I2C.h>

int motorLoopCounter = 0;
bool motorTest = false;
int lastMotorMillis = 0;
int motorSwitchRate = 2000;

#include "objectDetection.h"

LiquidCrystal_I2C lcd(0x27, 16, 2);
#include "lcdScreens.h"

#define buttonR 7
#define buttonUp 6
#define buttonDown 5
#define buttonL 4

int menuState = 0;
int powerMenuCursor = 0;

int refreshRate = 200;
int lastMillis = 0;

#include "motorDriver.h"

void setup() {
  Serial.begin(9600);
  Serial.println("Boot Start");

  Wire.begin(9, 8);

  lcd.init();
  lcd.backlight();

  pinMode(buttonL, INPUT_PULLUP);
  pinMode(buttonUp, INPUT_PULLUP);
  pinMode(buttonDown, INPUT_PULLUP);
  pinMode(buttonR, INPUT_PULLUP);

  motorSetup();
  INA219Setup();

  Serial.println("Boot End");
}

void loop() {
  if (motorTest) {
    motorTestControl();
  } else {
    motorControl(0, 0, 0);
    motorControl(1, 0, 0);
    motorLoopCounter = 0;
  }

  if (menuState == 0) {
    if (!digitalRead(buttonDown)) {
      menuState = 1;
      while (!digitalRead(buttonDown)) {
      }
    } else if (!digitalRead(buttonUp)) {
      menuState = 3;
      while (!digitalRead(buttonUp)) {
      }
    }
  } else if (menuState == 1) {
    if (!digitalRead(buttonR)) {
      motorTest = !motorTest;
      while (!digitalRead(buttonR)) {
      }
    }
    if (!digitalRead(buttonDown)) {
      menuState = 2;
      while (!digitalRead(buttonDown)) {
      }
    } else if (!digitalRead(buttonUp)) {
      menuState = 0;
      while (!digitalRead(buttonUp)) {
      }
    }
  } else if (menuState == 2) {
    if (!digitalRead(buttonDown)) {
      menuState = 3;
      while (!digitalRead(buttonDown)) {
      }
    } else if (!digitalRead(buttonUp)) {
      menuState = 1;
      while (!digitalRead(buttonUp)) {
      }
    }
  } else if (menuState == 3) {
    if (!digitalRead(buttonR)) {
      if (powerMenuCursor == 2) {
        powerMenuCursor = 0;
      } else {
        powerMenuCursor++;
      }
      while (!digitalRead(buttonR)) {
      }
    } else if (!digitalRead(buttonL)) {
      if (powerMenuCursor == 0) {
        powerMenuCursor = 2;
      } else {
        powerMenuCursor--;
      }
      while (!digitalRead(buttonL)) {
      }
    }
    if (!digitalRead(buttonDown)) {
      menuState = 0;
      while (!digitalRead(buttonDown)) {
      }
    } else if (!digitalRead(buttonUp)) {
      menuState = 2;
      while (!digitalRead(buttonUp)) {
      }
    }
  }

  if ((millis() - lastMillis) > refreshRate) {
    lastMillis = millis();
    switch (menuState) {
      case 0:
        displayHomescreen();
        break;
      case 1:
        displayMenu1();
        break;
      case 2:
        displaySonarTest("", "", "");
        break;
      case 3:
        INA219Read();
        displayCurrentTest(powerMenuCursor, currentSensorReading);
        break;
    }
  }
}

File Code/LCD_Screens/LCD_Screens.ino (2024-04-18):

#include <LiquidCrystal_I2C.h>

LiquidCrystal_I2C lcd(0x27, 16, 2);

void setup() {
  Serial.begin(9600);
  Serial.println("Boot Start");

  lcd.init();
  lcd.backlight();

  Serial.println("Boot End");

}

void loop() {
  Serial.println("Home Screen");
  displayHomescreen();
  delay(10000);

  Serial.println("Menu 1");
  displayMenu1();
  delay(10000);

  Serial.println("Menu 2");
  displayMenu2();
  delay(10000);

  Serial.println("Menu 3");
  displayMenu3();
  delay(10000);

  Serial.println("Sonar Test");
  displaySonarTest(15, 22, 56);
  delay(10000);

  Serial.println("Button Test");
  displayButtonTest(1, 1, 0 ,1);
  delay(10000);

  Serial.println("Engine Test L F");
  displayEngineTestLeftForward();
  delay(10000);

  Serial.println("Engine Test L R");
  displayEngineTestLeftReverse();
  delay(10000);

  Serial.println("Engine Test R F");
  displayEngineTestRightForward();
  delay(10000);

  Serial.println("Engine Test R R");
  displayEngineTestRightReverse();
  delay(10000);

  Serial.println("Engine Test 2 F");
  displayEngineTestForward();
  delay(10000);

  Serial.println("Engine Test 2 R");
  displayEngineTestReverse();
  delay(10000);

  Serial.println("Current Test");
  displayCurrentTest(3.43);
  delay(10000);

}

void displayHomescreen() {
  lcd.clear();
  lcd.setCursor(0,0);
  lcd.print("RobotMower");
  lcd.setCursor(0,1);
  lcd.print("V1.0.0");
}

void displayMenu1() {
  lcd.clear();
  lcd.setCursor(0,0);
  lcd.print("Sonar Test");
  lcd.setCursor(0,1);
  lcd.print("Button Test");
}

void displayMenu2() {
  lcd.clear();
  lcd.setCursor(0,0);
  lcd.print("Button Test");
  lcd.setCursor(0,1);
  lcd.print("Engine Test");
}

void displayMenu3() {
  lcd.clear();
  lcd.setCursor(0,0);
  lcd.print("Engine Test");
  lcd.setCursor(0,1);
  lcd.print("Current Test");
}

void displayCurrentTest(float currentBat) {
  lcd.clear();
  lcd.setCursor(0,0);
  lcd.print("Current Test");
  lcd.setCursor(0,1);
  lcd.print("Bat: ");
  lcd.setCursor(5, 1);
  lcd.print(currentBat);
}

void displayEngineTestLeftForward() {
  lcd.clear();
  lcd.setCursor(0,0);
  lcd.print("Engine Test");
  lcd.setCursor(0,1);
  lcd.print("Left Motor F");
}

void displayEngineTestLeftReverse() {
  lcd.clear();
  lcd.setCursor(0,0);
  lcd.print("Engine Test");
  lcd.setCursor(0,1);
  lcd.print("Left Motor R");
}

void displayEngineTestRightForward() {
  lcd.clear();
  lcd.setCursor(0,0);
  lcd.print("Engine Test");
  lcd.setCursor(0,1);
  lcd.print("Right Motor F");
}

void displayEngineTestRightReverse() {
  lcd.clear();
  lcd.setCursor(0,0);
  lcd.print("Engine Test");
  lcd.setCursor(0,1);
  lcd.print("Right Motor R");
}

void displayEngineTestForward() {
  lcd.clear();
  lcd.setCursor(0,0);
  lcd.print("Engine Test");
  lcd.setCursor(0,1);
  lcd.print("2 Motor F");
}

void displayEngineTestReverse() {
  lcd.clear();
  lcd.setCursor(0,0);
  lcd.print("Engine Test");
  lcd.setCursor(0,1);
  lcd.print("2 Motor R");
}

void displaySonarTest(int lValue, int mValue, int rValue) {
  lcd.clear();
  lcd.setCursor(0,0);
  lcd.print("  L    M    R  ");
  lcd.setCursor(2,1);
  lcd.print(lValue);
  lcd.setCursor(7, 1);
  lcd.print(mValue);
  lcd.setCursor(12, 1);
  lcd.print(rValue);
}

void displayButtonTest(bool button1Value, bool button2Value, bool button3Value, bool button4Value) {
  lcd.clear();
  lcd.setCursor(0,0);
  lcd.print("  1    2    3    4");
  lcd.setCursor(2,1);
  lcd.print(button1Value);
  lcd.setCursor(7, 1);
  lcd.print(button2Value);
  lcd.setCursor(12, 1);
  lcd.print(button3Value);
  lcd.setCursor(14, 1);
  lcd.print(button4Value);
}

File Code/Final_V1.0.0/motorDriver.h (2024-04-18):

#define hbridgeENA 35
#define hbridgeIN1 36
#define hbridgeIN2 37

#define hbridgeENB 39
#define hbridgeIN3 40
#define hbridgeIN4 41

void motorSetup() {
  pinMode(hbridgeENA, OUTPUT);
  pinMode(hbridgeENB, OUTPUT);
  pinMode(hbridgeIN1, OUTPUT);
  pinMode(hbridgeIN2, OUTPUT);
  pinMode(hbridgeIN3, OUTPUT);
  pinMode(hbridgeIN4, OUTPUT);

  digitalWrite(hbridgeENA, 0);
  digitalWrite(hbridgeENB, 0);
  digitalWrite(hbridgeIN1, 0);
  digitalWrite(hbridgeIN2, 0);
  digitalWrite(hbridgeIN3, 0);
  digitalWrite(hbridgeIN4, 0);
}

void motorControl(int motorSelect, bool driveDirection, int speed) {
  if (motorSelect == 0) {
    if (speed == 0) {
      digitalWrite(hbridgeENA, 0);
      digitalWrite(hbridgeIN1, 0);
      digitalWrite(hbridgeIN2, 0);
    } else {
      analogWrite(hbridgeENA, speed);
      digitalWrite(hbridgeIN1, driveDirection);
      digitalWrite(hbridgeIN2, !driveDirection);
    }
  } else if (motorSelect == 1) {
    if (speed == 0) {
      digitalWrite(hbridgeENB, 0);
      digitalWrite(hbridgeIN3, 0);
      digitalWrite(hbridgeIN4, 0);
    } else {
      analogWrite(hbridgeENB, speed);
      digitalWrite(hbridgeIN3, driveDirection);
      digitalWrite(hbridgeIN4, !driveDirection);
    }
  }
}

void motorTestControl() {
  if ((millis() - lastMotorMillis) > motorSwitchRate) {
    lastMotorMillis = millis();
    if (motorLoopCounter < 5) {
      Serial.print("Motor loop counter: ");
      Serial.println(motorLoopCounter);
      switch (motorLoopCounter) {
        case 0:
          motorControl(0, 1, 255);
          motorControl(1, 1, 255);
          break;
        case 1:
          motorControl(0, 1, 100);
          motorControl(1, 1, 100);
          break;
        case 2:
          motorControl(0, 0, 255);
          motorControl(1, 0, 255);
          break;
        case 3:
          motorControl(0, 0, 100);
          motorControl(1, 0, 100);
          break;
        case 4:
          motorControl(0, 0, 0);
          motorControl(1, 0, 0);
          break;
      }
      motorLoopCounter++;
    } else {
      motorLoopCounter = 0;
    }
  }
}

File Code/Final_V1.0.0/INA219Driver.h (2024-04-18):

#include <INA.h>

const uint32_t SHUNT_MICRO_OHM{
    6000}; ///< Shunt resistance in Micro-Ohm, e.g. 100000 is 0.1 Ohm
const uint16_t MAXIMUM_AMPS{
    2};                  ///< Max expected amps, clamped from 1A to a max of 1022A
uint8_t devicesFound{0}; ///< Number of INAs found
INA_Class INA;           ///< INA class instantiation to use EEPROM

void INA219Setup() {
  Serial.print("\n\nDisplay INA Readings V1.0.8\n");
  Serial.print(" - Searching & Initializing INA devices\n");

  devicesFound = INA.begin(MAXIMUM_AMPS, SHUNT_MICRO_OHM); // Expected max Amp & shunt resistance
  while (devicesFound == 0)
  {
    Serial.println(F("No INA device found, retrying in 10 seconds..."));
    delay(10000);                                            // Wait 10 seconds before retrying
    devicesFound = INA.begin(MAXIMUM_AMPS, SHUNT_MICRO_OHM); // Expected max Amp & shunt resistance
  }                                                          // while no devices detected

  Serial.print(F(" - Detected "));
  Serial.print(devicesFound);
  Serial.println(F(" INA devices on the I2C bus"));

  INA.reset(0);
  INA.reset(1);
  INA.reset(2);

  INA.begin(5, 6000, 0);
  INA.begin(MAXIMUM_AMPS, 40000, 1);
  INA.begin(MAXIMUM_AMPS, 40000, 2);

  INA.setBusConversion(8500);             // Maximum conversion time 8.244ms
  INA.setShuntConversion(8500);           // Maximum conversion time 8.244ms
  INA.setAveraging(1024);                 // Average each reading n-times
  INA.setMode(INA_MODE_CONTINUOUS_BOTH);  // Bus/shunt measured continuously
  INA.alertOnBusOverVoltage(true, 12000); // Trigger alert if over 12V on bus
}

void INA219Read() {
  for (uint8_t i = 0; i < devicesFound; i++) // Loop through all devices
  {
    currentSensorReading[i][0] = float(INA.getBusMilliVolts(i) / 1000.0);   
    currentSensorReading[i][1] = float(INA.getShuntMicroVolts(i) / 1000.0); 
    currentSensorReading[i][2] = float(INA.getBusMicroAmps(i) / 1000.0);  
    currentSensorReading[i][3] = float(INA.getBusMicroWatts(i) / 1000000.0); 

    Serial.print(i);
    Serial.print("|");
    Serial.print(currentSensorReading[i][0]);
    Serial.print("|");
    Serial.print(currentSensorReading[i][1]);
    Serial.print("|");
    Serial.print(currentSensorReading[i][2]);
    Serial.print("|");
    Serial.println(currentSensorReading[i][3]);

  }
}

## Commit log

2024-02-28 Eagle library
    Added the Eagle Library with currently only the ATtiny84 in SOIC and DIP format
2024-02-28 Added the base Schematics
2024-02-29 Adding current Schematics
    [Main_Schematic.sch]
2024-02-29 Changed names
    [Main_Schematic.sch]
2024-02-29 adding the individual schematics and the main library for eagle
2024-03-07 Adding Schematics
    [Main_Schematic.sch]
2024-03-07 Programming
    Added the explanations for programming the ATtiny84 and for programming the ESP32S3
2024-03-07 Create Gerbers
2024-03-07 Gerbers
    Adding the gerbers of the ultrasonic pcb and the MCU pcb
2024-03-08 Adding the BOMs
    [HC-SR04_Middle-Man v9 BOM.csv, MCU v14 BOM.csv, Main BOM.xlsx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]
2024-03-10 changed 12mOhm and 39mOhm resistors
    [Main BOM.xlsx]
2024-03-19 reichelt bpom
    [Reichelt BOM.csv]
2024-03-21 Update I2C_Scanning file
2024-03-27 added the basic sketches for reading the ultrasonic sensor and for the basic I2C communication
2024-04-17 added INA219 functionality to motor test program
2024-04-18 update of the schematic
2024-04-18 adding the schematic and board files from fusion and the libraries
    [ATtiny84 Base Schematic v2.sch, ESP32S3 Base Schematic v1.sch, HC-SR04_Middle-Man v14.brd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]
2024-04-18 updates to ESP32s3.md

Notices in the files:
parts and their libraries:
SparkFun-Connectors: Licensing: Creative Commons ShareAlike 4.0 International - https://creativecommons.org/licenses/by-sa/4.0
